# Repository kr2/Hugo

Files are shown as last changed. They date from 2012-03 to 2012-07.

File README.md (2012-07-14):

NOT ALL PARTS ARE TESTED

At the moment the config.scad and metric.scad file aren't implemented consistently. So if you want to change something look in the scad file of the corresponding part and if the desired setting already depends on the config.scad or metric.scad check the appropriate.

It is always recommend to check the stl files before printing. If you have problems slicing the stl fils with Slic3r try fixing them with http://cloud.netfabb.com/ (for Skeinforge the files should work out of the box).

Wiki: http://reprap.org/wiki/Hugo

Brief
=====
This is Hugo. Named after Hugo de Vries who introduced the term "mutation".

First of I would like to thank Joachim (jsturm) who started this project in the first place and did almost the entire testing of the parts. The entire design is done in OpenSCAD and all files are hosted on https://github.com/kr2/Hugo.

It is a derivative of the original Printrbot by abdrumm, but all parts are redesigned and improved.

Some Improvements are:

-   The main parts are tested ;)
-   Nut traps everywhere
-   Optional cross braces
-   Centered y belt
-   Carriage with 3 bearings
-   Belt tensioner for x and y Belts
-   Additional base in y direction

Instructions
============
There is a H-assembly.scad, which is not perfect but shows a complete setup of the Printer.
To view this  H-assembly.scad I recommend to use the actual developer release of OpenScad e.g. http://www.onewheelweb.com/static/openscad/OpenSCAD-2012.02.19-Installer.exe and to set the value for "Turn off render at ... elements" [edit->Preferences] to a higher value (I use 200000).

So there are several prebuilt stl files to discover and to put your own assembly together or you build your own via OpenSCAD.

In general if you print H-set1.stl and H-set2.stl you should have all mandatory parts to build the Printer. If you also print H-set3.stl you should be able to setup the entire printer similar to the one shown in H-assembly.scad. It is recommend to use LMXXUU or igus linear Bearings but the H-set7_PLA.scad contains printable linear bearings. This bearings should be printed in PLA because it is harder then ABS.

Credits
=======
-   JSturm for everything especially for the Testing
-   Thimo for the patches

Sources
=======
Bar clamp:
Bar clamp by Josef Průša
https://github.com/prusajr/PrusaMendel

Bearing Guide:
Bearing Guide by GregFrost
https://github.com/GregFrost/PrusaMendel

Also some modules and metric files from the two above.

Extruder:
Greg's Wade reloaded - Guidler, Tilt Screws, Fishbone Gears by jonaskuehling
http://www.thingiverse.com/thing:18379

Printrbot:
THE Printrbot by abdrumm
http://www.thingiverse.com/thing:16990

Thanks to all of them.
(If I missed someone I am sorry, plz contact me.)

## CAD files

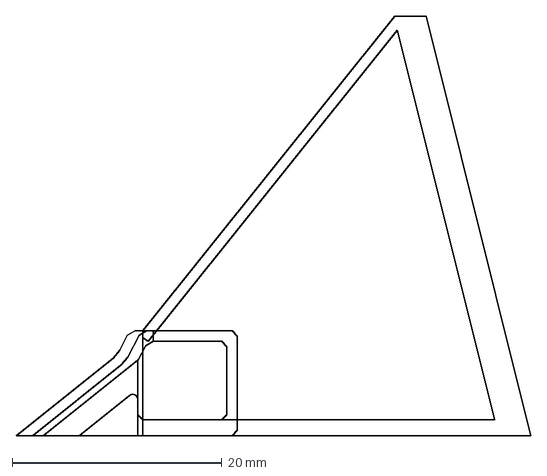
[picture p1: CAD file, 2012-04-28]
src/fanOutlet.dxf
49.1 x 40.0 mm

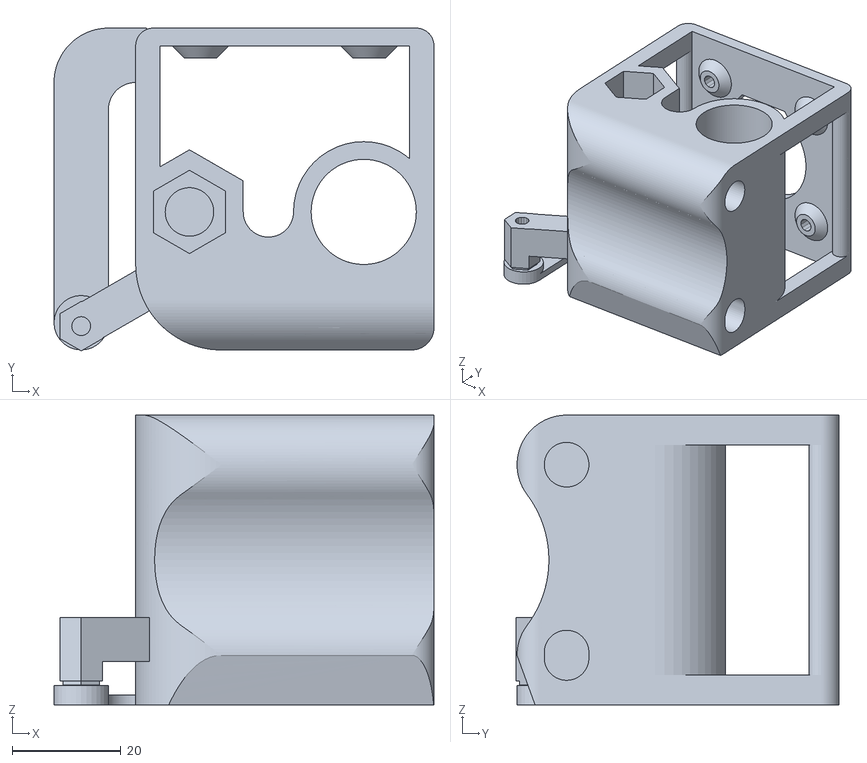
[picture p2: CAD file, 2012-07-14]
stl/Hugo+/H-X-End_left.stl
69.8 x 59.3 x 53.2

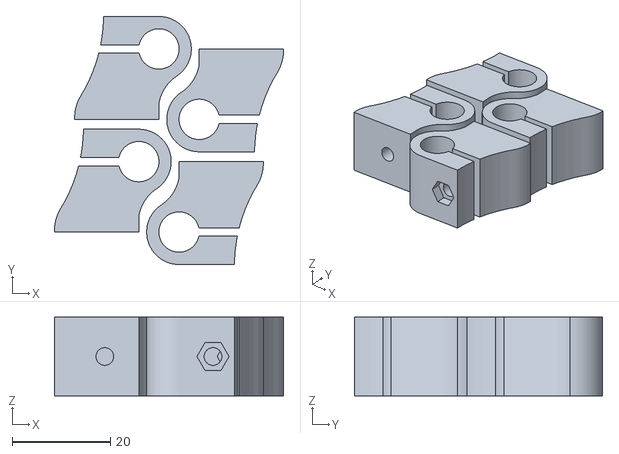
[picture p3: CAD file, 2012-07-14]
stl/Hugo_improved/H-Y-BarEnd_Set.stl
46.6 x 50.4 x 16.0

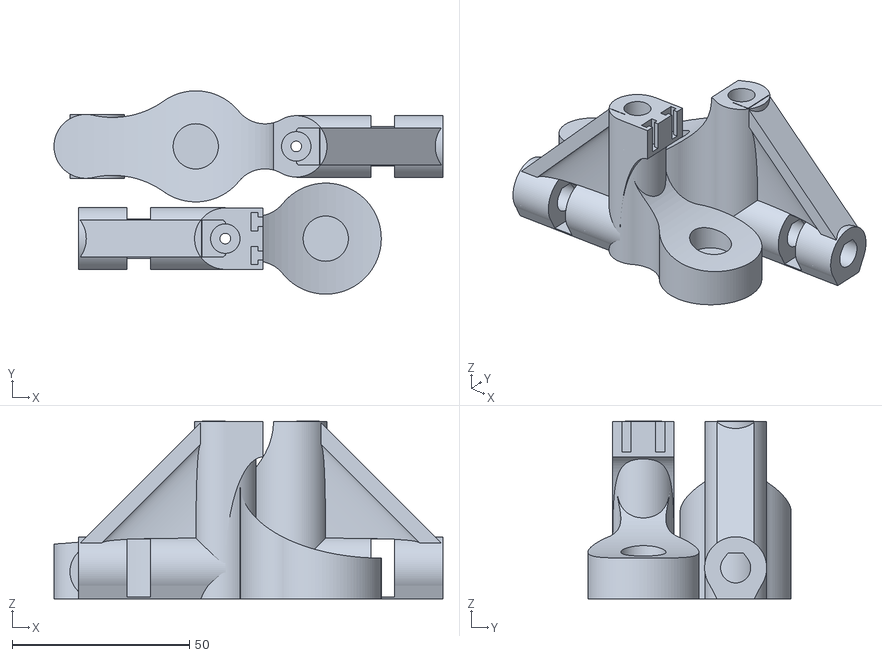
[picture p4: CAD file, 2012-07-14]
stl/Hugo_standard/H-Z-End_Set1.stl
109.6 x 57.3 x 50.1

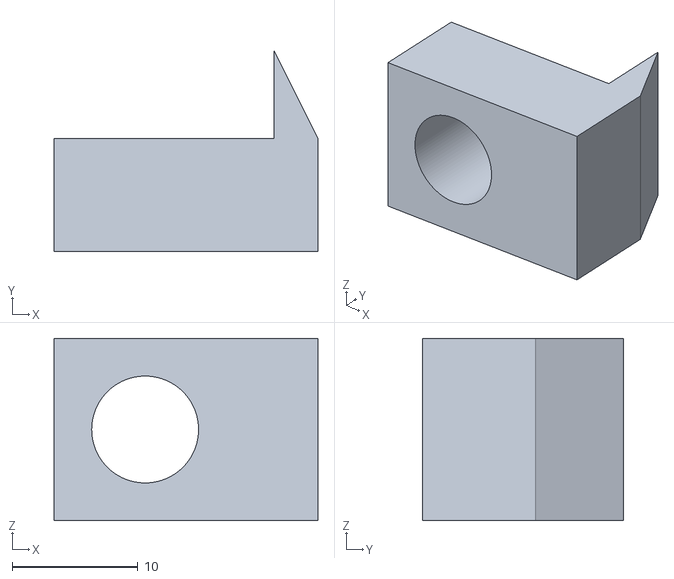
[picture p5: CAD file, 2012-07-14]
stl/pb_standard/TableClamp_alternativ.stl
21.0 x 16.0 x 14.5

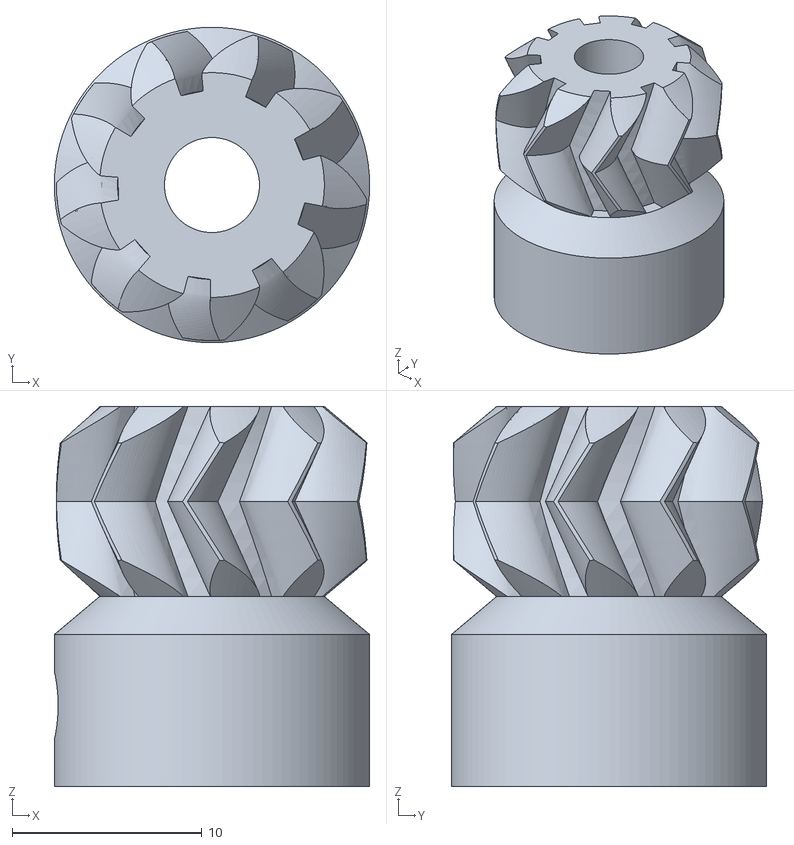
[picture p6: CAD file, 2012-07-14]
stl/Hugo+/H-GregWadeGears_Smal.stl
16.6 x 16.6 x 20.0

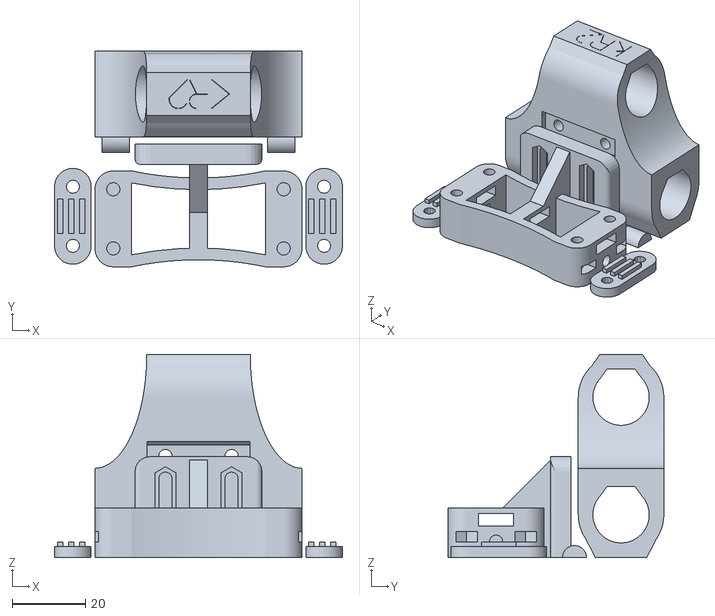
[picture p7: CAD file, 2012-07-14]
stl/Hugo_improved/H-X-Carriager_Set.stl
78.4 x 58.7 x 55.3

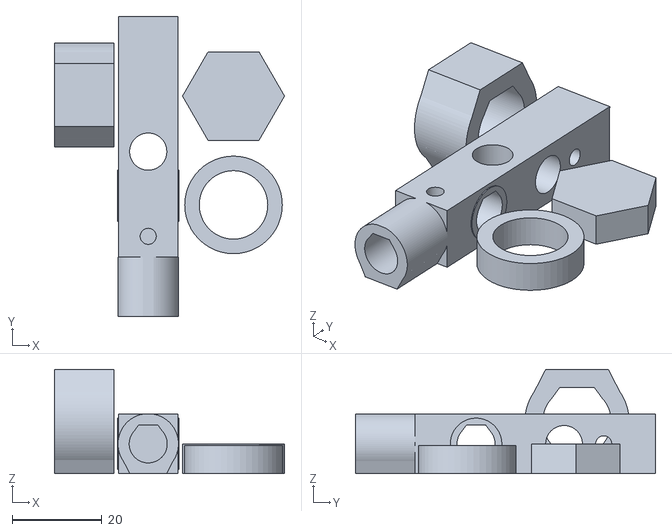
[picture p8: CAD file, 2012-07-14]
stl/pb_standard/H-TestObject.stl
51.4 x 67.0 x 23.3

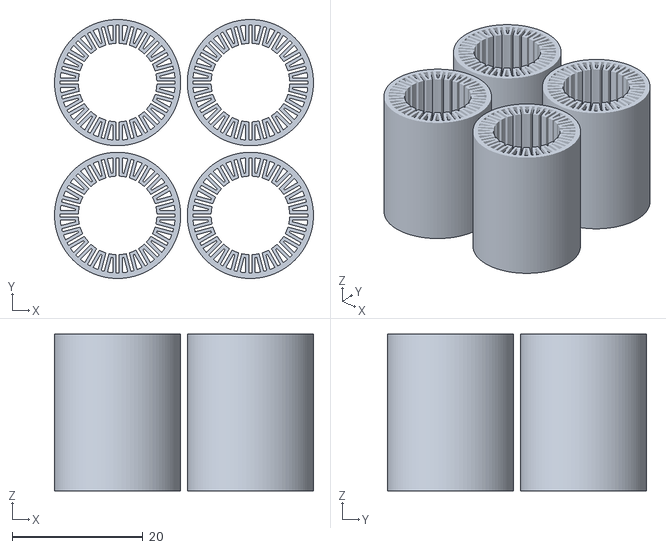
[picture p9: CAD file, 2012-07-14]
stl/Hugo+/H-Set7_PLA.stl
39.6 x 39.6 x 24.0

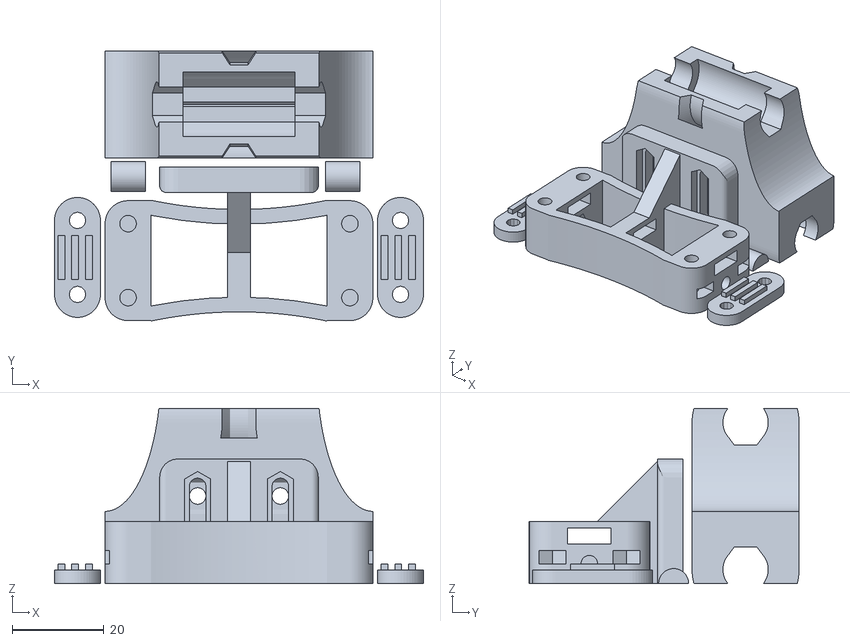
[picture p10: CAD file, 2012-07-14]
stl/Hugo_improved/H-X-Carriager_alternativ2_Set.stl
80.3 x 58.8 x 38.1

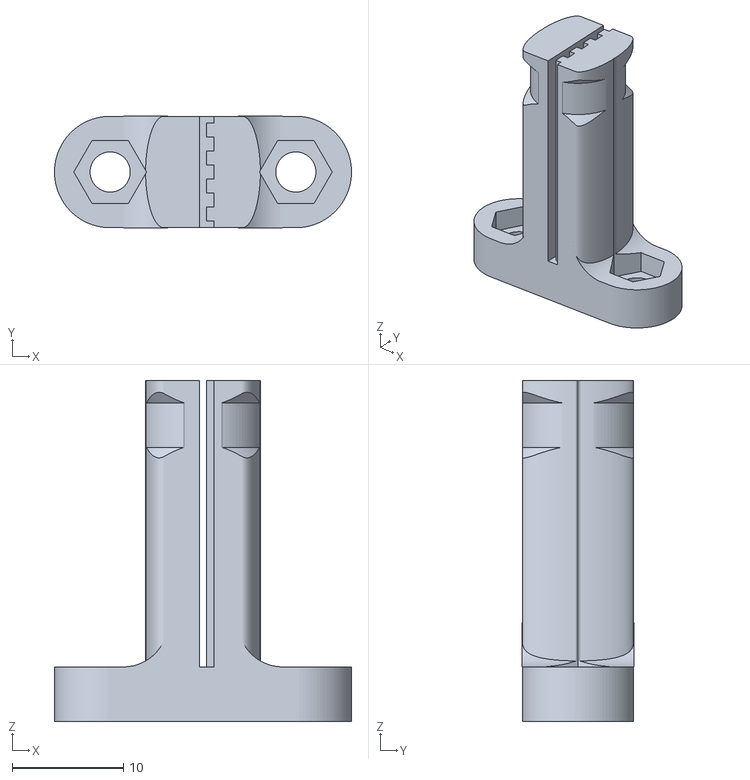
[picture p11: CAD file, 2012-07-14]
stl/Hugo_standard/H-Y-beltClamp_alternativ.stl
26.7 x 10.0 x 30.6

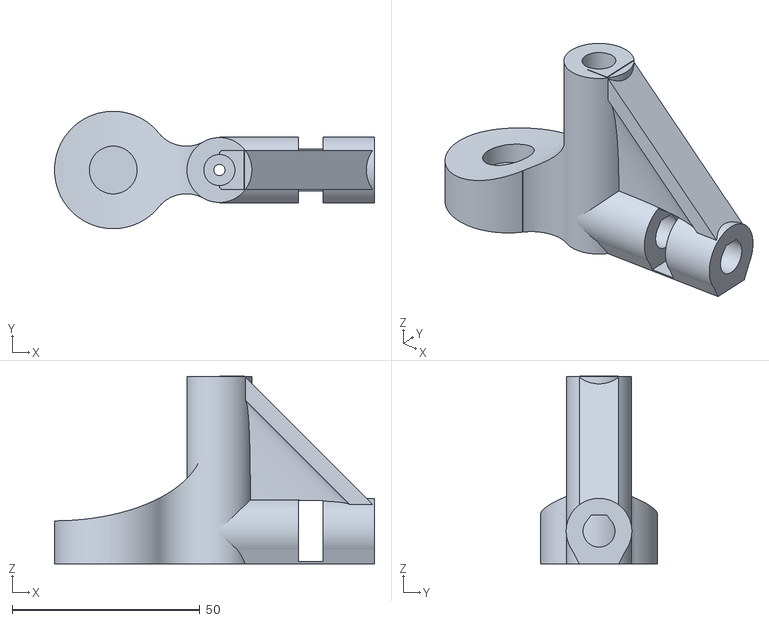
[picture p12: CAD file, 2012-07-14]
stl/pb_standard/H-Z-End_NoEnds.stl
85.3 x 31.3 x 50.1

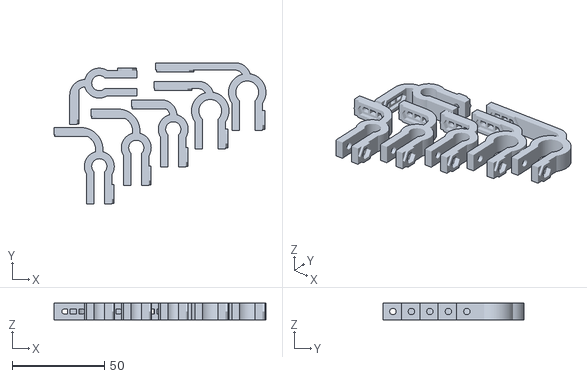
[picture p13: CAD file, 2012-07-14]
stl/Hugo+/H-EndstopHolder_set1.stl
114.7 x 76.5 x 9.01

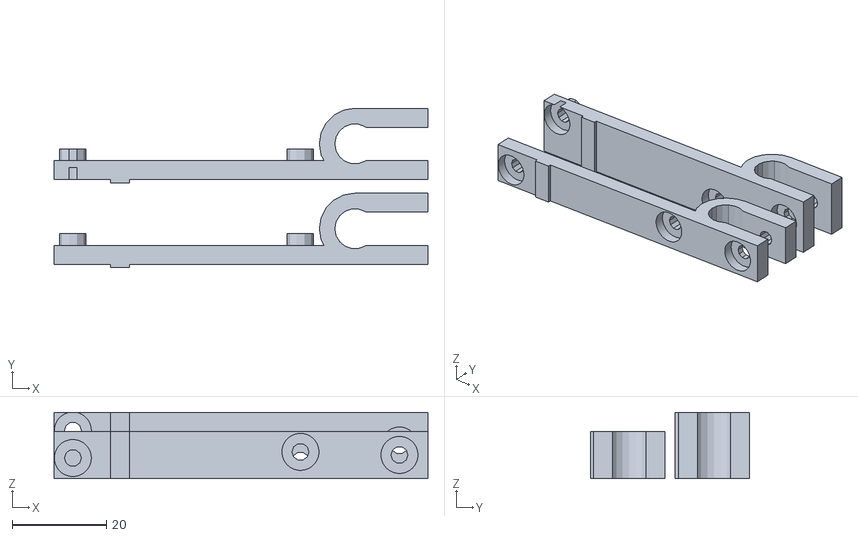
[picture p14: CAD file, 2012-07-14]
stl/Hugo_improved/RampsHolder.stl
79.3 x 33.8 x 14.0

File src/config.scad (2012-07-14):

/* config [c]
 * Copyright (c) 2012 by Krallinger Sebastian [s.krallinger+cc@gmail.com]
 * Dual-licensed under
 * Creative Commons Attribution-ShareAlike 3.0 (CC BY-SA) [http://creativecommons.org/licenses/by-sa/3.0/]
 * and
 * LGPL v2 or later [http://www.gnu.org/licenses/].
 */

include <metric.scad>

/* --------- REFERENCE ----------
Standard Printrbot dimensions.
- T5 Belt
- T5/10 Pulleys
*/
//include <config/pb_standard.scad>


/*
Changes:
- T2.5 belt
- T2.5/20 Pulley
*/
//include <config/Hugo_standard.scad>


/*
Changes:
- 12 mm Z-Axis
- T2.5 belt
- T2.5/12 Pulley
- Printvoule: 300x300x300 mm
- x Axis rod dist increased (from 25.38 mm to 32)
*/
//include <config/Hugo+.scad>


/*
Changes:
- HTD 3M belt
- 3M/12 Pulley
- x Axis rod dist increased (from 25.38 mm to 32)
*/
include <config/Hugo_improved.scad>

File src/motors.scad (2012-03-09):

// Copyright 2010 D1plo1d

// This library is dual licensed under the GPL 3.0 and the GNU Lesser General Public License as per http://creativecommons.org/licenses/LGPL/2.1/ .

mm_per_inch = 25.4;


//generates a motor mount for the specified nema standard #.
module stepper_motor_mount(nema_standard,slide_distance=0, mochup=true, tolerance=0) {
	//dimensions from:
	// http://www.numberfactory.com/NEMA%20Motor%20Dimensions.htm
	if (nema_standard == 17)
	{
		_stepper_motor_mount(
			motor_shaft_diameter = 0.1968*mm_per_inch,
			motor_shaft_length   = 0.945*mm_per_inch,
			pilot_diameter       = 0.866*mm_per_inch,
			pilot_length         = 0.80*mm_per_inch,
			mounting_bolt_circle = 1.725*mm_per_inch,
			bolt_hole_size       = 3.5,
			bolt_hole_distance   = 1.220*mm_per_inch,
			slide_distance       = slide_distance,
			mochup               = mochup,
			tolerance            =tolerance);
	}
	if (nema_standard == 23)
	{
		_stepper_motor_mount(
			motor_shaft_diameter = 0.250*mm_per_inch,
			motor_shaft_length   = 0.81*mm_per_inch,
			pilot_diameter       = 1.500*mm_per_inch,
			pilot_length         = 0.062*mm_per_inch,
			mounting_bolt_circle = 2.625*mm_per_inch,
			bolt_hole_size       = 0.195*mm_per_inch,
			bolt_hole_distance   = 1.856*mm_per_inch,
			slide_distance       = slide_distance,
			mochup               = mochup,
			tolerance            =tolerance);
	}
	
}


//inner mehod for creating a stepper motor mount of any dimensions
module _stepper_motor_mount(
	motor_shaft_diameter,
	motor_shaft_length,
	pilot_diameter,
	pilot_length,
	mounting_bolt_circle,
	bolt_hole_size,
	bolt_hole_distance,
	slide_distance = 0,
	motor_length = 40, //arbitray - not standardized
	mochup,
	tolerance = 0
)
{
	union()
	{
	// == centered mount points ==
	//mounting circle inset
	translate([0,slide_distance/2,0]) circle(r = pilot_diameter/2 + tolerance);
	square([pilot_diameter,slide_distance],center=true);
	translate([0,-slide_distance/2,0]) circle(r = pilot_diameter/2 + tolerance);

	//todo: motor shaft hole
	
	//mounting screw holes
	for (x = [-1,1])
	{
		for (y = [-1,1])
		{
			translate([x*bolt_hole_distance/2,y*bolt_hole_distance/2,0])
			{
				translate([0,slide_distance/2,0]) circle(bolt_hole_size/2 + tolerance);
				translate([0,-slide_distance/2,0]) circle(bolt_hole_size/2 + tolerance);
				square([bolt_hole_size+2*tolerance,slide_distance],center=true);
			}
		}
	}
	// == motor mock-up ==
	//motor box
	if (mochup == true)
	{
		color("DimGray"){
			translate([0,0,-5]) cylinder(h = 5, r = pilot_diameter/2);
			translate(v=[0,0,-motor_length/2])
			{
				cube(size=[bolt_hole_distance+bolt_hole_size+5,bolt_hole_distance+bolt_hole_size+5,motor_length], center = true);
			}
			//shaft
			translate(v=[0,0,-(motor_length-motor_shaft_length-2)/2])
			{
				cylinder(r=motor_shaft_diameter/2,h=motor_length+motor_shaft_length--1, center = true);
			}
		}
	}
	}
}

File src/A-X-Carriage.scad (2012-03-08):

/* A-X-Carriage [Xc]
 * Copyright (c) 2012 by Krallinger Sebastian [s.krallinger+cc@gmail.com]
 * 
 * Creative Commons Attribution-ShareAlike 3.0 (CC BY-SA) [http://creativecommons.org/licenses/by-sa/3.0/]
 * original desing by abdrumm for the PrintrBot
 */

include <units.scad>;
include <metric.scad>
include <roundEdges.scad>
include <utilities.scad>
include <barbell.scad>
use <A-Y-beltClamp.scad>

/*------------------------------------general---------------------------------*/
Xc_mode = "print";  // can be print or inspect [overlays the Xc_model with the original Xc_model] (uncomment next line)
//Xc_mode = "inspect";
//$fn=96;

Xc_axis_dist                 = 25.38;
Xc_genWallThickness          = 2.5;
Xc_strongWallThickness       = 5;

Xc_slot_width                = 5;

Xc_horizontalSuportThickness = 0.3;
Xc_verticalSupportThickness  = 0.7;

/*------------------------------------linear bearings-------------------------*/
Xc_lber_length             = 24;
Xc_lber_diam               = 15.3;


/*------------------------------------notch-----------------------------------*/
// connecot notch to the xtruder holder
Xc_notch_width             = 5.4;
Xc_notch_depth             = 1.2;
Xc_notch_lengt             = 24 + 2.5 + 0.5;

/*------------------------------------xtruder carriag holes-------------------*/
Xc_holes_diam              = m4_diameter;
Xc_holes_dist              = 18;

/*------------------------------------rod-------------------------------------*/
Xc_rod_diam                = 8.5;

/*------------------------------------belt------------------------------------*/
Xc_belt_axisXc_ydir_dist   = 30; // distece between center x axis and nerest belt edge
Xc_belt_axisXc_zdir_offset = -5; // distece between center x axis and toothed side of the belt in z dir
Xc_belt_thickness          = 2.5;
Xc_belt_width              = 6 + 1;
Xc_belt_teethDist          = 5;
Xc_belt_teethDepth         = 1.5;
Xc_belt_tolerance          = [1,2,1]; //[t,w,-1]

Xc_beltClamp_depth         = 10;


/*------------------------------------internals-------------------------------*/
// belt connector
Xc_beltClamp_beltHole      = [Xc_belt_thickness+Xc_belt_tolerance[0],Xc_belt_width+Xc_belt_tolerance[1],-1];
Xc_beltClamp_center_height = Xc_genWallThickness+m3_nut_wallDist;
Xc_beltClamp_width         = Xc_belt_width+Xc_belt_tolerance[1]+m3_diameter*2+m3_nut_diameter;
Xc_beltClamp_heigth        = Xc_belt_thickness+Xc_belt_tolerance[0]+Xc_genWallThickness+m3_nut_wallDist;

Xc_xdir                    = Xc_axis_dist+Xc_lber_diam+2*Xc_genWallThickness;
Xc_ydir                    = Xc_lber_diam+2*Xc_genWallThickness;
Xc_zdir                    = Xc_lber_length*2+Xc_genWallThickness;

Xc_matCoutout_scale        = (Xc_lber_length/2)/(Xc_axis_dist/2+Xc_lber_diam/2+Xc_genWallThickness); // material coutout scale
Xc_matCoutout_rounded_r    = Xc_xdir/2;


Xc_belt_axisDist           = distance1D(Xc_belt_axisXc_ydir_dist+Xc_belt_width/2,Xc_belt_axisXc_zdir_offset+(Xc_beltClamp_center_height+Xc_beltClamp_beltHole[0])/2);
Xc_belt_holder_angle       = atan((Xc_belt_axisXc_zdir_offset+(Xc_beltClamp_center_height+Xc_beltClamp_beltHole[0])/2)/(Xc_belt_axisXc_ydir_dist+Xc_belt_width/2));



module A_x_Carriage(hasSupport = true, hasBeltConnector = true) {

	
	difference() {
		union(){
			for (i=[-Xc_axis_dist/2,Xc_axis_dist/2]) 
			translate([i, 0, 0]) 
				cylinder(r=Xc_lber_diam/2+Xc_genWallThickness, h=Xc_lber_length*2+Xc_genWallThickness, center=false);
			translate([0, 0, Xc_lber_length+Xc_genWallThickness/2]) 
				cube(size=[Xc_axis_dist, Xc_lber_diam+2*Xc_genWallThickness, Xc_lber_length*2+Xc_genWallThickness], center=true);

			if (hasBeltConnector) {
				union() {
					intersection() {
						translate([-Xc_axis_dist/2, 0, 0]) 
						rotate(a=90-Xc_belt_holder_angle,v=Z) 
						rotate(a=-90,v=Y)
						linear_extrude(height=Xc_zdir)
							barbell(Xc_beltClamp_width/2,Xc_beltClamp_width/2,Xc_zdir*0.5,Xc_zdir*0.55,Xc_zdir+2*OS);
			
						linear_extrude(height=Xc_zdir)
						translate([-Xc_axis_dist/2, 0, 0]) 
						rotate(a=-Xc_belt_holder_angle,v=Z) 
						rotate(a=-90,v=[0,0,1]) 
							barbell((Xc_lber_diam+Xc_genWallThickness*2)/2,Xc_beltClamp_width/2,Xc_belt_axisXc_ydir_dist*0.35,Xc_belt_axisXc_ydir_dist*0.3,Xc_belt_axisDist);
					}

					// place for tabel for conectors
					for (i=[0,Xc_zdir- Xc_beltClamp_depth]) 
					translate([-(Xc_axis_dist/2+Xc_belt_axisXc_zdir_offset), -(Xc_belt_axisXc_ydir_dist+Xc_belt_width/2), 0]){//belt center
						translate([-Xc_beltClamp_width, -(Xc_beltClamp_width-Xc_beltClamp_depth)/2, i]) {
							cube(size=[Xc_beltClamp_width, Xc_beltClamp_width-Xc_beltClamp_depth,Xc_beltClamp_depth], center=false);
						}
						for (c=[-(Xc_beltClamp_width-Xc_beltClamp_depth)/2,(Xc_beltClamp_width-Xc_beltClamp_depth)/2])
						translate([-Xc_beltClamp_width-(Xc_beltClamp_center_height+Xc_beltClamp_beltHole[0])/2, c, i+Xc_beltClamp_depth/2])
						rotate(a=90,v=Y) 
							cylinder(r=Xc_beltClamp_depth/2, h=Xc_beltClamp_width, center=false);
					}
				}
				
				
				
				
			
			}
		}
		union(){
			if (hasBeltConnector) {
				// top coutoff
				translate([-(Xc_axis_dist/2+Xc_belt_axisXc_zdir_offset), -(Xc_belt_axisXc_ydir_dist+Xc_belt_width/2), 0]){ // center belt 
					// tabel center coutout
					*translate([-Xc_beltClamp_width, -Xc_beltClamp_width/2, +Xc_beltClamp_depth]) {
						cube(size=[Xc_beltClamp_width, Xc_beltClamp_width, Xc_zdir-Xc_beltClamp_depth*2], center=false);
						translate([Xc_beltClamp_width/2, Xc_beltClamp_width, 0]) 
							roundEdge(_a=0,_r=Xc_beltClamp_width/2,_l=Xc_zdir-2*Xc_beltClamp_depth,_fn=100);
					}
					// tabel top coutout
					translate([-Xc_beltClamp_width-Xc_beltClamp_heigth, -Xc_beltClamp_width/2-OS, -OS]) {
						cube(size=[Xc_beltClamp_width, Xc_beltClamp_width+OS*2, Xc_zdir+OS*2], center=false);
						translate([Xc_beltClamp_width/8*7, Xc_beltClamp_width, 0]) 
							roundEdge(_a=0,_r=Xc_beltClamp_width/8,_l=Xc_zdir+2*OS,_fn=100);
					}

					//belt coutout
					for (i=[-OS,Xc_zdir- Xc_beltClamp_depth-OS])
					translate([-(Xc_belt_thickness+Xc_belt_tolerance[0]), -(Xc_belt_width+Xc_belt_tolerance[1])/2, i])  
						cube(size=[Xc_belt_thickness+Xc_belt_tolerance[0], Xc_belt_width+Xc_belt_tolerance[1], Xc_beltClamp_depth+2*OS], center=false);

					translate([-Xc_beltClamp_width, -(Xc_belt_width+Xc_belt_tolerance[1])/2, Xc_beltClamp_depth])  
						cube(size=[Xc_beltClamp_width*2, Xc_belt_width+Xc_belt_tolerance[1], Xc_zdir- Xc_beltClamp_depth*2], center=false);
					
				} 
				
				translate([-(Xc_axis_dist/2+Xc_belt_axisXc_zdir_offset), -(Xc_belt_axisXc_ydir_dist+Xc_belt_width/2), 0]){//belt center bottom
					for (i=[0,Xc_zdir- Xc_beltClamp_depth]) {
						
						for (c=[-(Xc_beltClamp_width-Xc_beltClamp_depth)/2,(Xc_beltClamp_width-Xc_beltClamp_depth)/2]){
							// belt fixiating screw holes
							translate([-Xc_beltClamp_width/2-Xc_beltClamp_beltHole[0], c, i+Xc_beltClamp_depth/2])
							rotate(a=90,v=Y) 
								cylinder(r=m3_diameter/2, h=Xc_beltClamp_width+OS*2, center=false,$fn=12);
							// eleongeteated nuttraps
							translate([-Xc_beltClamp_beltHole[0]-Xc_beltClamp_center_height/4-m3_elongNtt_height/2, c, i+Xc_beltClamp_depth/2])
							rotate(a=90,v=Y) 
								cylinder(r=m3_elongNtt_diameter/2, h=m3_elongNtt_height, center=false,$fn=6); 
							
						}

						// belt tentener holes
						translate([-(Xc_beltClamp_center_height)/2-Xc_beltClamp_beltHole[0], 0, i-OS])
							cylinder(r=m3_diameter/2, h=Xc_beltClamp_depth+2*OS, center=false,$fn=12);
					} 
					//belt tenter holes
					for (i=[Xc_beltClamp_depth- m3_nut_heigth, Xc_zdir-Xc_beltClamp_depth-OS]) 
					translate([-(Xc_beltClamp_center_height)/2-Xc_beltClamp_beltHole[0], 0, i])
					rotate(a=30,v=[0,0,1]) 
						cylinder(r=m3_nut_diameter/2, h=m3_nut_heigth+OS, center=false,$fn=6); 

					// elengeteated nuttraps
					for (i=[-OS,Xc_zdir-Xc_beltClamp_depth/2]) 
					for (c=[-(Xc_beltClamp_width-Xc_beltClamp_depth)/2,(Xc_beltClamp_width-Xc_beltClamp_depth)/2])// center screws
					translate([-Xc_beltClamp_beltHole[0]-Xc_beltClamp_center_height/4-m3_elongNtt_height/2, c- m3_elongNtt_wallDist/2, i]) 
						cube(size=[m3_elongNtt_height, m3_elongNtt_wallDist, Xc_beltClamp_depth], center=false);
				}
				
				
			}

			// slot
			translate([0, 0, Xc_zdir/2])
				cube(size=[Xc_axis_dist, Xc_slot_width, Xc_zdir+2*OS], center=true); 

			//bearin coutout
			translate([-Xc_axis_dist/2, 0, -OS])
				difference() {
					cylinder(r=Xc_lber_diam/2, h=Xc_lber_length*2+Xc_genWallThickness+2*OS, center=false);
				 	*translate([0, 0, Xc_lber_length])
				 		_bearingStop(); 
				} 
			translate([Xc_axis_dist/2, 0, -OS])
				difference() {
					cylinder(r=Xc_lber_diam/2, h=Xc_lber_length*2+Xc_genWallThickness+2*OS, center=false);
				 	*translate([0, 0, Xc_lber_length/2])
				 		_bearingStop(); 
				}
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

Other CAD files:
stl/Hugo_standard/H-X-Carriager_alternativ2.stl
stl/pb_standard/H-Z-End_Left-MotorCutout.stl
stl/Hugo+/H-GregWadeGears_Spacer.stl
src/A-X-End.scad
src/A-Z-End.scad
src/BearingGuide.scad
src/GregsWade_v4.scad
src/H-Assembly.scad
src/H-BarClamp.scad
src/H-BarClampCross.scad
src/H-Base.scad
src/H-BearingGuide.scad
src/H-BedClamp.scad
src/H-EndstopHolder.scad
src/H-Fan.scad
src/H-Fanduct.scad
src/H-GregWadeGears.scad
src/H-Set1.scad
src/H-Set1_2.scad
src/H-Set2.scad
src/H-Set3.scad
src/H-Set3_2.scad
src/H-Set4.scad
src/H-Set7_PLA.scad
src/H-TestObject.scad
src/H-X-Carriager.scad
src/H-X-Carriager_alternativ.scad
src/H-X-Carriager_alternativ2.scad
src/H-X-End.scad
src/H-Xtruder-Mount.scad
src/H-Y-BarEnd.scad
src/H-Y-beltClamp.scad
src/H-Y-beltClamp_alternativ.scad
src/H-Y-beltDivert.scad
src/H-Y-supportFootEnd.scad
src/H-Z-Coupling.scad
src/H-Z-Coupling_alternativ.scad
src/H-Z-End.scad
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

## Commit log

2012-03-03 overhang fixed (cylindical start removed(optinal available))
    [pb-X-End.scad]
2012-03-03 adjustabel z screw holder with spring added
    [pb-X-End.scad]
2012-03-03 added elongetated hole for the lower x axis
    [pb-X-End.scad]
2012-03-03 fixed spring
    [pb-X-End.scad]
2012-03-03 fixed some metrics
    [pb-X-End.scad]
2012-03-03 added metic and rounded edges
    [metric.scad, roundEdges.scad]
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2012-03-04 Y-axis belt tensioner added
    [pRb-Y-beltClamp.scad, set1.scad]
2012-03-04 1st line fix
    [pRb-Y-beltClamp.scad]
2012-03-04 fixed idler hole. (reduced segments of the cylinder and increased the hole diameter)
    [pRb-X-End.scad]
2012-03-05 barbell outsourced and utilities.scad added
    [barbell.scad, pRb-X-End.scad, utilities.scad]
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2012-03-05 carriage interly reworked
    [pRb-X-Carriage.scad]
2012-03-05 nut slot tolerance added
    [pRb-Y-beltClamp.scad]
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2012-03-05 some material coutoffs and mad it mor pritnable
    [pRb-Y-beltClamp.scad]
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2012-03-05 some metrics changed and added
    [metric.scad, pRb-Y-beltClamp.scad]
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2012-03-05 made it easier to print i hope
    [pRb-Y-beltClamp.scad]
2012-03-06 gregfrost endstop file added
    [gregs-endstop-holder.scad]
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2012-03-06 endstop switch holder added
    [pRb-enstop-holder.scad]
2012-03-06 coutout size increaset for the cabels of the extruder nozzel
    [pRb-Xtruder-Mount.scad]
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2012-03-07 Z End added but OpenScad compile error
    [pRb-Z-End.scad]
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2012-03-07 removed bearing stop and added slot
    [pRb-X-Carriage.scad]
2012-03-07 increasd wall thickness of bearing holder an nut holder
    [metric.scad, pRb-X-End.scad]
2012-03-07 metrix fixed
    [pRb-enstop-holder.scad]
2012-03-07 added x axis assembly
    [bearing-guide.scad, motors.scad, pRb-Z-End.scad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]
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2012-03-07 y belt diverter added
    [pRb-Y-beltDivert.scad]
2012-03-07 y support foot end added
    [pRb-Y-supportFootEnd.scad]
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2012-03-07 fixed metrics
    [pRb-Y-supportFootEnd.scad]
2012-03-07 !!!Not finished jet!!! base added
    [pRb-base.scad]
2012-03-08 base first compleat implementation
    [pRb-base.scad]
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2012-03-08 prepeard for cross brace
    [pRb-Z-End.scad]
2012-03-08 clamp for cross brace
    [bar-clamp-cross.scad]
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2012-03-08 clean up and assembly
    [H-X-Carriage.scad, H-X-End.scad, H-Xtruder-Mount.scad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]
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2012-03-09 fixed print
    [H-Xtruder-Mount.scad, H-base.scad]
2012-03-09 y support foot added to assembly
    [H-Xtruder-Mount.scad, H-Y-supportFootEnd.scad, H-assembly.scad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]
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2012-03-09 color and function check
    [H-assembly.scad, basicMetalParts.scad]
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2012-03-09 fixed assembly
    [H-Z-End.scad, H-assembly.scad, H-bar-clamp-cross.scad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]
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2012-03-10 m4 nut diameter fixed for carriage
    [metric.scad]
2012-03-10 fixd support distance
    [H-X-Carriage.scad]
2012-03-10 fixed notch metrix so the xtruder mount fits better
    [H-X-Carriage.scad]
2012-03-10 decreased idler hole sligly for stronger fit
    [H-X-End.scad]
2012-03-10 increas x dir holes diameter sligtly for easyer fit and reinforced hole walls for this x dir holes
    [H-X-End.scad]
2012-03-10 fixd hole diameters
    [H-Xtruder-Mount.scad]
2012-03-10 fised screw hole dieameters
    [H-Xtruder-Mount.scad]
2012-03-10 removet lber since it is and should be in config
    [metric.scad]
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2012-03-10 reinforced z dir bases
    [H-base.scad]
2012-03-10 replaced x dir holse with teardrops
    [H-base.scad]
2012-03-10 replaces bearing holder hols by teardrops
    [H-base.scad]
2012-03-10 incresed moto hole coutout for easyer fit
    [H-X-End.scad]
2012-03-10 fixed motor connector
    [H-base.scad]
2012-03-10 fixed z dir offset of the belt
    [H-X-Carriage.scad]
2012-03-10 fixed misspelling
    [H-Z-End.scad]
2012-03-10 fixed var naming
    [H-Z-Coupling.scad]
2012-03-11 added coupling to assambly
    [H-Z-Coupling.scad, H-assembly.scad]
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2012-03-11 fixed license
    [H-Y-supportFootEnd.scad]
2012-03-11 added info field to BOM
    [H-X-End.scad, H-Y-BarEnd.scad, H-Z-End.scad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]
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2012-03-14 incresed x dir wall for better screw fit
    [H-base.scad]
2012-03-14 fixet z axis dist
    [H-base.scad]
2012-03-14 added parameter for distance beween z axis and motor axis
    [H-base.scad]
2012-03-14 added z motor distance holder
    [H-base.scad]
2012-03-14 switch off eleongetated hole of the lower x axis
    [H-X-End.scad]
2012-03-14 incerased width of elongetated hole support by addinga aditional param
    [H-enstop-holder.scad]
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2012-03-14 added elongetated hole for lower x axis to compasate the dirfferent print directions
    [H-X-Carriage.scad]
2012-03-15 entered the changes done by jsturm. mainly renaming of stuff.
    [BearingGuide.scad, BearingGuide.stl, BearingGuide_x3.stl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]
2012-03-15 removed x cross brace
    [H-Z-End.scad, H-assembly.scad]
2012-03-15 fixed problem with outline
    [H-X-End.scad]
2012-03-15 removed correction factor by direct calculateion
    [H-X-End.scad]
2012-03-15 fixed center coutout
    [H-X-End.scad]
2012-03-15 made x end configurable via config.scad
    [H-X-End.scad, config.scad, metric.scad]
2012-03-16 made base partly configurable via config.scad
    [H-Base.scad, H-X-End.scad, config.scad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]
2012-03-16 made z end configurable via config.scad
    [H-Base.scad, H-Z-End.scad, config.scad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]
2012-03-16 made x carriage configurable via config.scad
    [H-X-Carriage.scad, config.scad]
2012-03-16 made x end more configurable via config.scad
    [H-X-End.scad, config.scad]
2012-03-16 fixed carriage for 2.5 belt and small pully
    [H-X-Carriage.scad]
2012-03-16 fixed connector
    [H-X-Carriage.scad]
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2012-03-16 fixed problem with bearing hole depth
    [H-Base.scad]
2012-03-16 prepared belt clamp for config.scad
    [H-Assembly.scad, H-Y-beltClamp.scad, config.scad]
2012-03-16 added extruder fixed stuff for reprapfab hotend prepared for assembly
    [gregs-wade-v4.scad]
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2012-03-16 removed build and added new pictures
    [BearingGuide.stl, BearingGuide_x3.stl, H-BarClamp.stl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]
2012-03-16 fixed base bearing holder hole
    [H-Base.scad, config.scad]
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2012-03-16 reinforced x end
    [H-Y-BarEnd.scad]
2012-03-16 removed threads from rod
    [basicMetalParts.scad]
2012-03-16 made configurable by config.scad
    [H-EndstopHolder.scad]
2012-03-16 fixed OS
    [H-Y-BarEnd.scad]
2012-03-16 fix missing wall
    [H-Y-beltDivert.scad]
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2012-03-16 pully added and fixed
    [pulley.scad]
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2012-03-16 fixed axis length
    [H-Assembly.scad]
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2012-03-16 fixed printset
    [H-Base.scad]
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2012-03-17 first draft of the fan
    [H-Fan.scad, fanOutlet.dxf]
2012-03-17 fixed y bearing holder
    [H-Base.scad, config.scad]
2012-03-17 increased motor size for base distance holder
    [config.scad]
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2012-03-17 fixed save range
    [H-Base.scad]
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2012-03-17 increased wall thickness and fixed nutt coutout for x dir
    [H-Z-End.scad]
2012-03-17 fixed some merge problems
    [H-X-Carriage.scad, config.scad]
2012-03-17 fixed idler hole pos
    [H-X-End.scad]
2012-03-17 fixed motor shaft diam
    [H-Z-Coupling.scad]
2012-03-17 finished up first fan version
    [H-Fan.scad, H-Fan.stl, fanOutlet.dxf]
2012-03-17 fixed clamps distance
    [H-Fan.scad, H-Fan.stl]
2012-03-18 fixed Sets
    [H-Base.scad, H-Fan.scad, H-Set1.scad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]
2012-03-18 added cone for axis hole entrance
    [H-Base.scad]
2012-03-18 increased motor screw holes diam
    [config.scad]
2012-03-18 increased axis holes diam
    [config.scad]
2012-03-18 fixed separator wall size for Slic3r
    [H-EndstopHolder.scad]
2012-03-18 increased axis holes diam
    Conflicts:
    src/config.scad
    [config.scad]
2012-03-18 cleaned out elongated hole
    [H-X-Carriage.scad]
2012-03-18 new lower bearing holder for carriage
    [H-X-Carriage.scad]
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2012-03-18 fixed axis dist
    [H-X-Carriage.scad]
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2012-03-19 connector clamp fixed print ability increased
    [H-Fanduct-set.stl, H-Fanduct.scad, fanOutlet.dxf]
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2012-03-23 fixed print set
    [ToothedLinearBearing_v1.scad]
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2012-03-23 fixed base wall thickness
    [H-Fanduct.scad, fanOutlet.dxf]
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2012-03-24 added tolerance to the lower bearing holder
    [H-X-Carriage.scad]
2012-03-26 fixed x axis distance
    [H-EndstopHolder.scad]
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2012-03-26 fixed support width for slic3r
    [H-EndstopHolder.scad]
2012-03-26 fixed 608ZZ diam for z end
    [metric.scad]
2012-03-26 fixed z direction roughrod diam
    [H-Z-End.scad]
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2012-03-26 increased lbearing length to counteract print errors
    [H-Base.scad]
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2012-03-26 chaged xtruder mount connector screws from m4 to m3
    [GregsWade_v4.scad]
2012-03-26 fixed nuttraps
    [GregsWade_v4.scad]
2012-03-26 fixed heatberral mount diam
    [GregsWade_v4.scad]
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2012-03-26 added 1.5 mm in x and z dir
    [H-Y-supportFootEnd.scad]
2012-03-27 decreased desitance of the y dir motor to the z axis
    [H-Base.scad]
2012-03-27 fixed origin offset
    [H-Calibration.scad]
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2012-03-27 fixed print and sets
    [H-Z-End.scad]
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2012-03-30 fixed new carriage
    [H-Assembly.scad]
2012-03-30 fixed intersect and made outsourced terdrop_flat
    [H-X-Carriager.scad]
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2012-03-30 fixed m2.5 nutt diameter
    [metric.scad]
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2012-03-30 fixed m3 nuttrap tolerance
    [metric.scad]
2012-03-30 fixed orientation of print output so it is always in the same direction as it is put together later on
    [H-Set1.scad, H-Set3.scad, H-X-End.scad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]
2012-03-30 fixed vertial support thickenss
    [H-Fanduct.scad]
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2012-03-30 fixed nuttrap
    [H-X-End.scad]
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2012-03-30 fixed bearinGuid test wall thicknes
    [H-TestObject.scad]
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2012-03-30 fixed orientation of print output so it is always in the same direction as it is put together later on
    src/H-Set3.scad
    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
    [H-Set1.scad, H-Set3.scad, H-X-End.scad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]
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2012-04-01 fixed nuttraps for y endstopholder
    [H-EndstopHolder.scad]
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2012-04-07 fixed for new bearing guid
    [config.scad]
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2012-04-07 fixed new bearing guid
    [H-X-End.scad]
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2012-04-07 fixed distance and zip tie holder
    [H-Y-beltClamp_alternativ.scad]
2012-04-08 fixed horizontal support thickness
    [H-BearingGuid.scad, H-BedClamp.scad, H-EndstopHolder.scad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]
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2012-04-10 increased distance between linear bearings in y direction for more stability
    [H-Base.scad]
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2012-04-14 removed teeht from one side and fixed distance
    [H-Y-beltClamp_alternativ.scad]
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2012-04-15 fixed assebly
    [H-X-End.scad]
2012-04-28 fixed nuttraps for rought rod for idler
    [GregsWade_v4.scad]
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2012-04-28 nuttrap fixed
    [GregsWadebits.scad]
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2012-04-28 outlet diameter increased for better fit of the heatberral
    [H-Fanduct.scad, fanOutlet.dxf]
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2012-04-28 see through hole fixed
    [H-X-Carriager.scad, H-X-Carriager_alternativ.scad]
2012-04-28 mode prefix fixed
    [H-Base.scad]
2012-04-28 mode fixed
    [H-Base.scad]
2012-05-03 increased wall thickness of the belt arm for more stability
    [H-X-Carriager.scad, H-X-Carriager_alternativ2.scad]
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2012-05-06 fixed error of z stop nuttrap with netfab and slic3r
    [H-X-End.scad]
2012-05-06 bug fix
    [Hugo_standard.scad]
2012-05-09 wrong bearing deviater diameter fixed and some typos
    [Hugo+.scad, Hugo_standard.scad, pb_standard.scad]
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2012-05-09 assembly fixed
    [H-X-End.scad]
2012-05-09 bugfix: belt holder grip generation
    [H-Y-beltClamp.scad]
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2012-05-10 fixed heatedbed size
    [H-Assembly.scad]
2012-05-13 fixed bearing diameter
    [GregsWade_v4.scad]
2012-05-13 bearing diameter fixed
    [H-Z-End.scad]
2012-05-17 increased wall diameter at motor screws so less different screws are needed
    [H-X-End.scad]
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2012-05-20 support cylinder bugfix
    [H-X-End.scad]
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2012-05-23 fixed missing hole ofsset of the smal holder
    [RampsHolder.scad]
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2012-05-25 removed nuttraps and added cutout for screw head
    [RampsHolder.scad]
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2012-06-05 fixed beltclamp mismatch
    [H-X-Carriager.scad, H-X-Carriager_alternativ.scad, H-X-Carriager_alternativ2.scad]
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2012-06-09 adde reinforcement
    [H-X-Carriager.scad, H-X-Carriager_alternativ2.scad]
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2012-06-11 fixed mode
    [H-Y-beltClamp_alternativ.scad]
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2012-06-23 bracket bug fix
    [H-X-Carriager.scad]
2012-06-23 increased notch depth and added backlash to the notch
    [H-X-Carriager.scad, H-X-Carriager_alternativ.scad, H-X-Carriager_alternativ2.scad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]
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2012-06-23 fixes Idler threaded road nuttraps to m3
    [GregsWade_v4.scad]
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2012-06-24 reinforced beltarm
    [H-X-Carriager.scad, H-X-Carriager_alternativ2.scad]
2012-06-29 nut sizes fixed patch by Thimp
    [H-EndstopHolder.scad]
2012-06-30 fixed wrong gears in set 4
    [GregWadeGears.scad, H-Set4.scad]
2012-06-30 fixed resolution
    [H-Set4.scad]
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2012-06-30 fixed resulution
    [H-GregWadeGears.scad]
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2012-07-01 obsolete, replaced by H-GregWadeGears.scad
    [GregWadeGears.scad]
2012-07-02 fixed screw head depth
    [H-GregWadeGears.scad]
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2012-07-12 fixed nuttrap (via patch by Thimo)
    [H-GregWadeGears.scad]
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2012-07-12 fixed spacer
    [H-Set4.scad]
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2012-07-12 fixed path delimiter
    [config.scad]
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
